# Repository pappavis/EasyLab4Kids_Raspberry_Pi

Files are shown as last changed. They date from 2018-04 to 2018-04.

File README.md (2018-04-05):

### EasyLab Arduino Robotauto
Arduino Robot alles-op-één bordje door **Michiel Erasmus** / EasyLab4Kids. Dit is die tegniese ontwerpe daarvan.<br/>

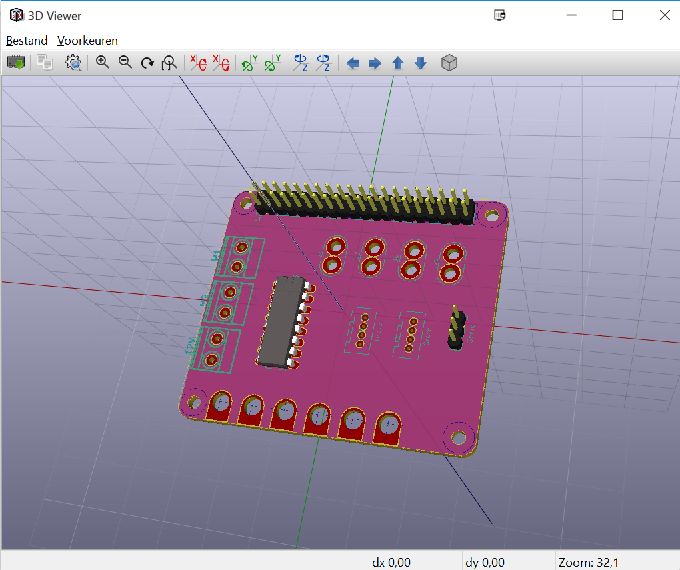
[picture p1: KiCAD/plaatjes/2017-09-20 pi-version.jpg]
<br/>

Credits:
---
**Ontwerp** deur Michiel Erasmus<br/>
**Kontak** thebapodcast@gmail.com<br/>
**Voorbeelde** https://www.facebook.com/EasyBlocks4Kids/<br/>
<br/>

EasyLab basis
---
Wat maak die EasyLab so besonder?<br/>
 - Robotauto op die planeet **MARS!!**
 - Volledig praktyk getest op kinders in Nederland<br/>
 - Beskikbaar met online lesmateriaal in Zuid-Afrikaans en Nederlands<br/>
 
EasyLab tegniese moontlikhede
---
Vir mense met 'n computer brein..<br/>
 - Support vir 2x robotmotors<br/>
 - 1x servo aansluiting<br/>
 - 2x Lynvolg snesore aansluitinge
 - 7x koperplaat aansluiting om maklik 'goedkope' aliexpress-sensore te kan gebruik<br/>
 - Skroefverbindinge vir robotmotors<br/>
 - GPIO en IO-poorte is almal beskikbaar
 - Beskikbaar in twee smake: Arduino en Raspberry Pi<br/>
 <br/>
 Elke EasyLab wordt ambagtelik in Den Haag, Nederland gemaak deur personeel met 'n mentaal of fysieke beperking. Dit help mee aan 'n menswaardig bestaan.<br/>

Self probeer?
---
kyk dan op https://www.facebook.com/EasyBlocks4Kids/ <br/>
<br/>
**EasyLab4Kids met LCD skerm en afstandmeting sensor;**<br/>
<br/>
<br/>
**EasyLab nuusgierige by CoderDojo Den Haag, Nederland [Jun-2017]**<br/>
<br/>
<br/>
Wil jy ook 'n EasyLab? Kontak thebapodcast@gmail.com<br/>
<br/>
<br/>
#easylab4kids #easyblocks4kids #arduinorobot
<br/>

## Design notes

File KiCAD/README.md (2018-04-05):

EasyLab: Raspberry Pi Edition
--
Dit is die printplaat ontwerp vir EasyLab pi editie.

**Credits:**<br/>
Ontwikkeld deur **Michiel Erasmus**.<br/>
Printplaat ontwerp deur **hemalchevli** op fiverr.com<br/>
<br/>
<br/>
**Copyrights**<br/>
GPLV2 license.<br/>
Noem my Michiel Erasmus in jouw credits.<br/>
<br/>
<br/>
<br/>
Printplaat;<br/>
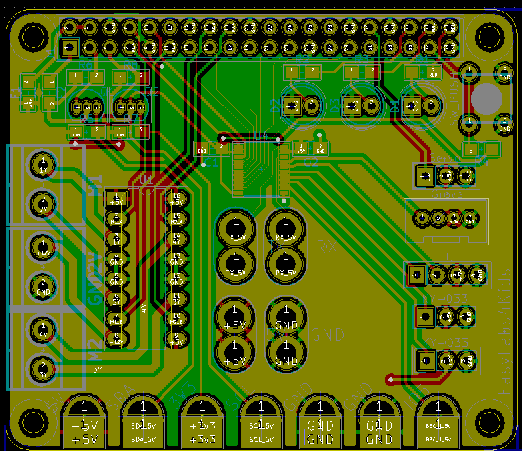
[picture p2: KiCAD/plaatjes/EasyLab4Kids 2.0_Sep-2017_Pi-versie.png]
<br/>
<br/>
#easylab4Kids #easyblocks4kids #erasmus-ict.nl #arduinorobot<br/>

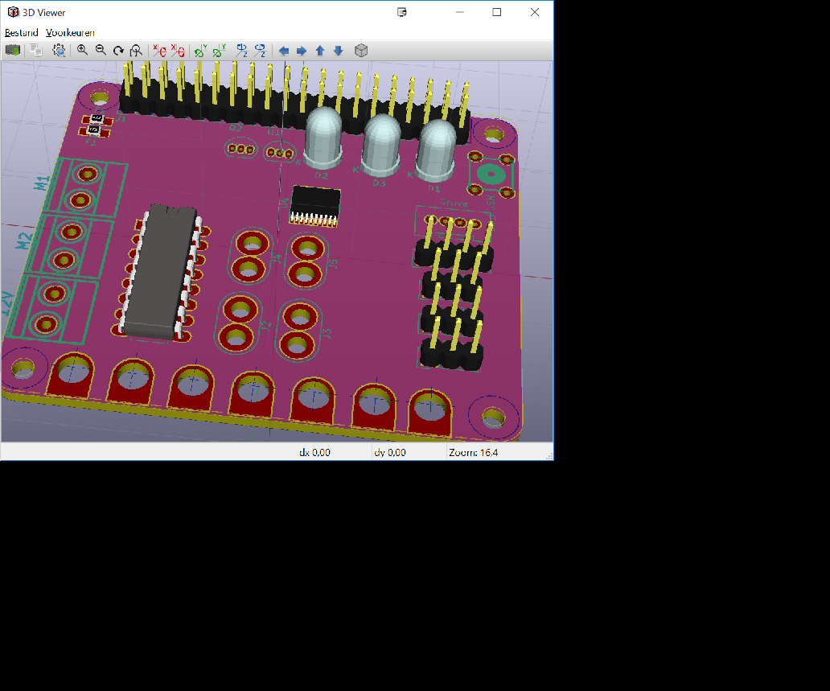
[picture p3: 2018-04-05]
KiCAD/plaatjes/__dev/EasyLab4Kids_Pi_0.0.2.png

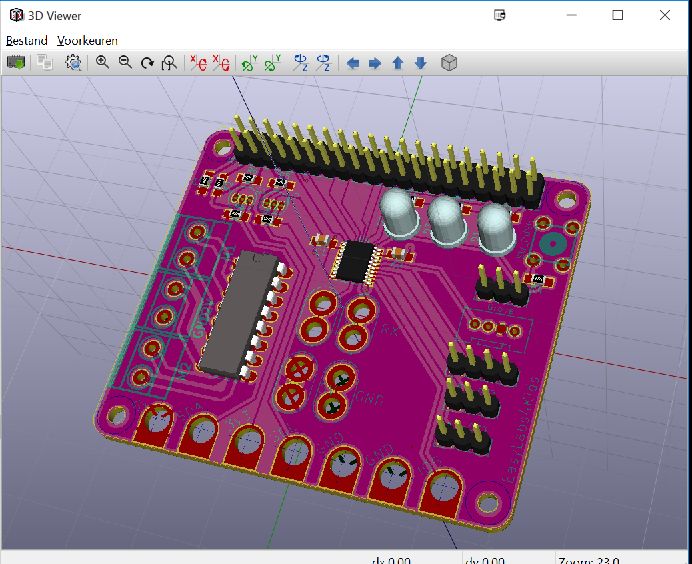
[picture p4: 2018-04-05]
KiCAD/plaatjes/EasyLab4Kids_Pi.jpg

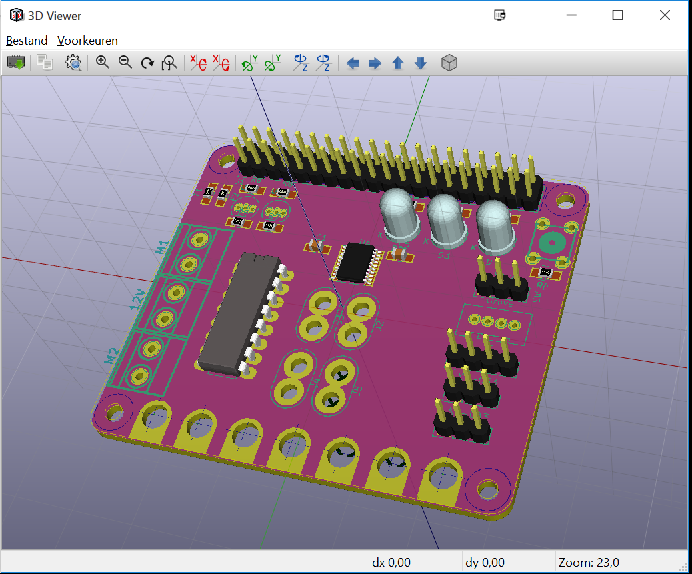
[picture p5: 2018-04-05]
KiCAD/plaatjes/__dev/EasyLab4Kids_Pi_0.0.3_update5.png

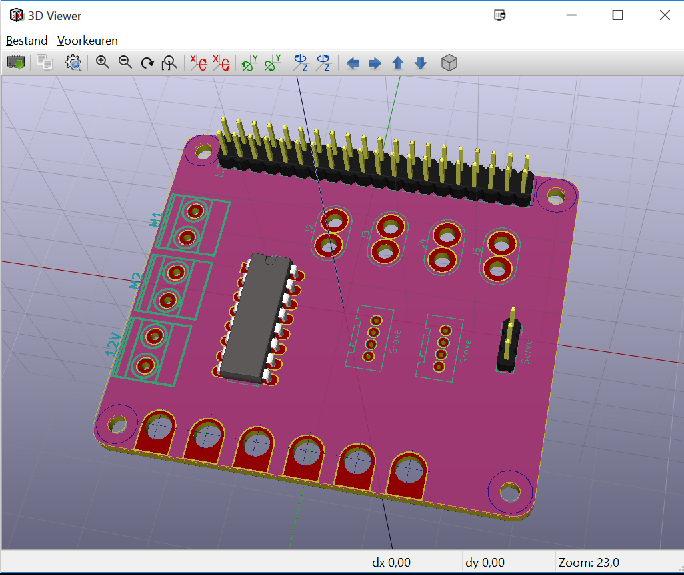
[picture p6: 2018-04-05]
KiCAD/plaatjes/__dev/EasyLab4Kids_Pi_0.0.1_update1.png

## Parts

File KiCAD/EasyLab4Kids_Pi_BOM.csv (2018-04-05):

Title | EasyLabs4Kids
Revision | 0
Date | 2017-09-21
Generated | 11-1-2018 13:44:21
Company
Comment 1 | Drawn by Hemal C [from Fiverr]
Comment 2
Comment 3
Comment 4
Total Parts | 40
Total Unique Parts | 26
Ref | Qty | Value | Footprint | MANF# | manf#
C1 C2 | 2 | 0.1uF | EasyLab4Kids_Pi:C_0805_HandSoldering
D3 D1 D2 | 3 | LED | EasyLab4Kids_Pi:LED-5MM
F1 | 1 | Polyfuse | EasyLab4Kids_Pi:R_0805_HandSoldering | 0ZCK0100FF2E
F2 | 1 | Polyfuse | EasyLab4Kids_Pi:R_0805_HandSoldering |  | 0ZCK0100FF2E
J6 | 1 | 5V | EasyLab4Kids_Pi:BBC_CONNECTOR
J7 J9 | 2 | GND | EasyLab4Kids_Pi:BBC_CONNECTOR
J8 | 1 | 3V3 | EasyLab4Kids_Pi:BBC_CONNECTOR
J10 J11 J18 | 3 | IO | EasyLab4Kids_Pi:BBC_CONNECTOR
J15 | 1 | M1 | EasyLab4Kids_Pi:mkds_1 | 5-2
J16 | 1 | 12V | EasyLab4Kids_Pi:mkds_1 | 5-2
J17 | 1 | M2 | EasyLab4Kids_Pi:mkds_1 | 5-2
J14 | 1 | Servo | EasyLab4Kids_Pi:Pin_Header_Straight_1x03
J2 | 1 | RX | EasyLab4Kids_Pi:Makey_conn
J3 | 1 | TX | EasyLab4Kids_Pi:Makey_conn
J4 | 1 | 5V | EasyLab4Kids_Pi:Makey_conn
J5 | 1 | GND | EasyLab4Kids_Pi:Makey_conn
J1 | 1 | RPi_Header | EasyLab4Kids_Pi:Pin_Header_Straight_2x20
J12 | 1 | Grove | EasyLab4Kids_Pi:grove_1x04
J19 | 1 | IO | EasyLab4Kids_Pi:Pin_Header_Straight_1x04
Q2 Q1 | 2 | 2N7000 | EasyLab4Kids_Pi:TO-92_Inline_Narrow_Oval
R3 R1 R2 | 3 | 330 | EasyLab4Kids_Pi:R_0805_HandSoldering
R4 R7 R8 R5 R6 | 5 | 10K | EasyLab4Kids_Pi:R_0805_HandSoldering
SW1 | 1 | SW_PUSH | EasyLab4Kids_Pi:PCB_PUSH_edit
U1 | 1 | L293D | EasyLab4Kids_Pi:DIP-16_W7.62mm_LongPads
U2 U3 | 2 | KY-033 | EasyLab4Kids_Pi:Pin_Header_Straight_1x03
U4 | 1 | TXB0108 | EasyLab4Kids_Pi:SSOP-20_4.4x6.5mm_Pitch0.65mm
BOM made with KICAD_BOM_WIZARD (https://github.com/HashDefineElectronics/KiCad_BOM_Wizard.git)
Generated 11-1-2018 13:44:21

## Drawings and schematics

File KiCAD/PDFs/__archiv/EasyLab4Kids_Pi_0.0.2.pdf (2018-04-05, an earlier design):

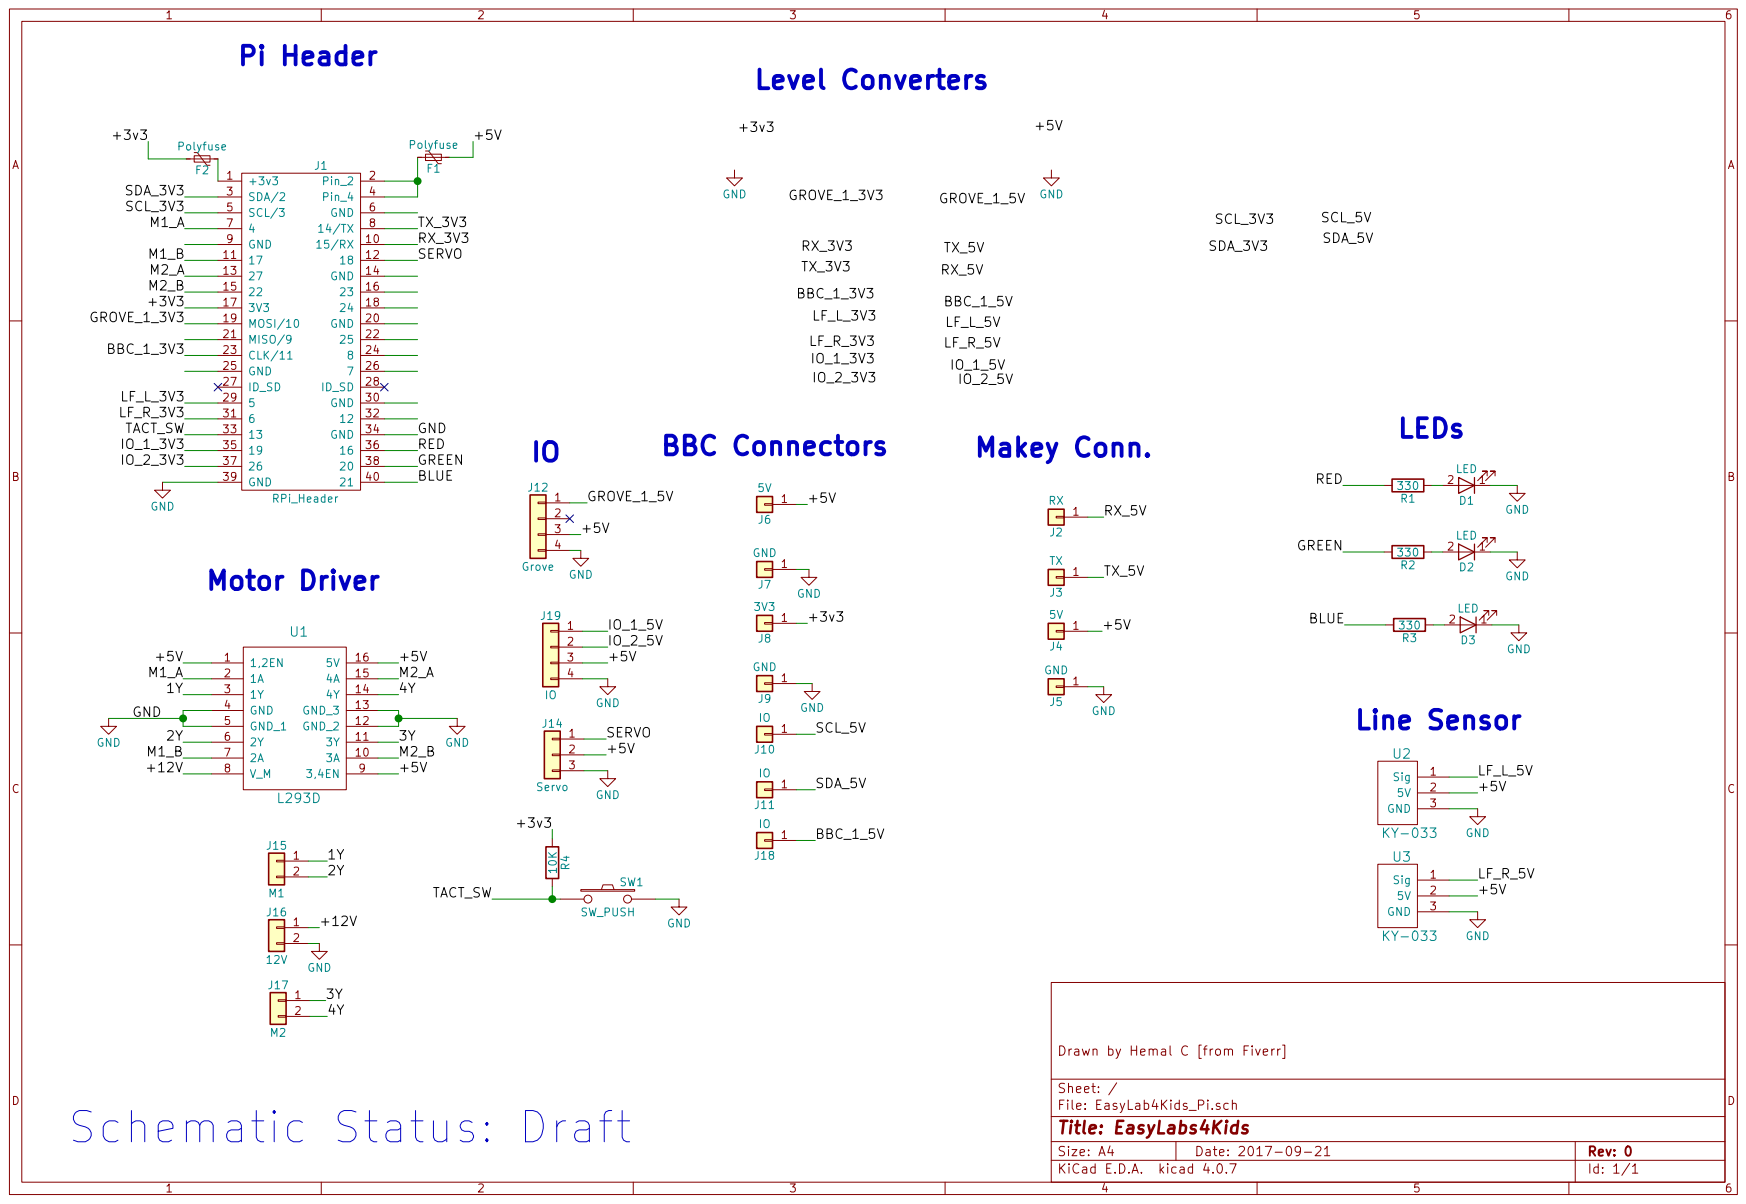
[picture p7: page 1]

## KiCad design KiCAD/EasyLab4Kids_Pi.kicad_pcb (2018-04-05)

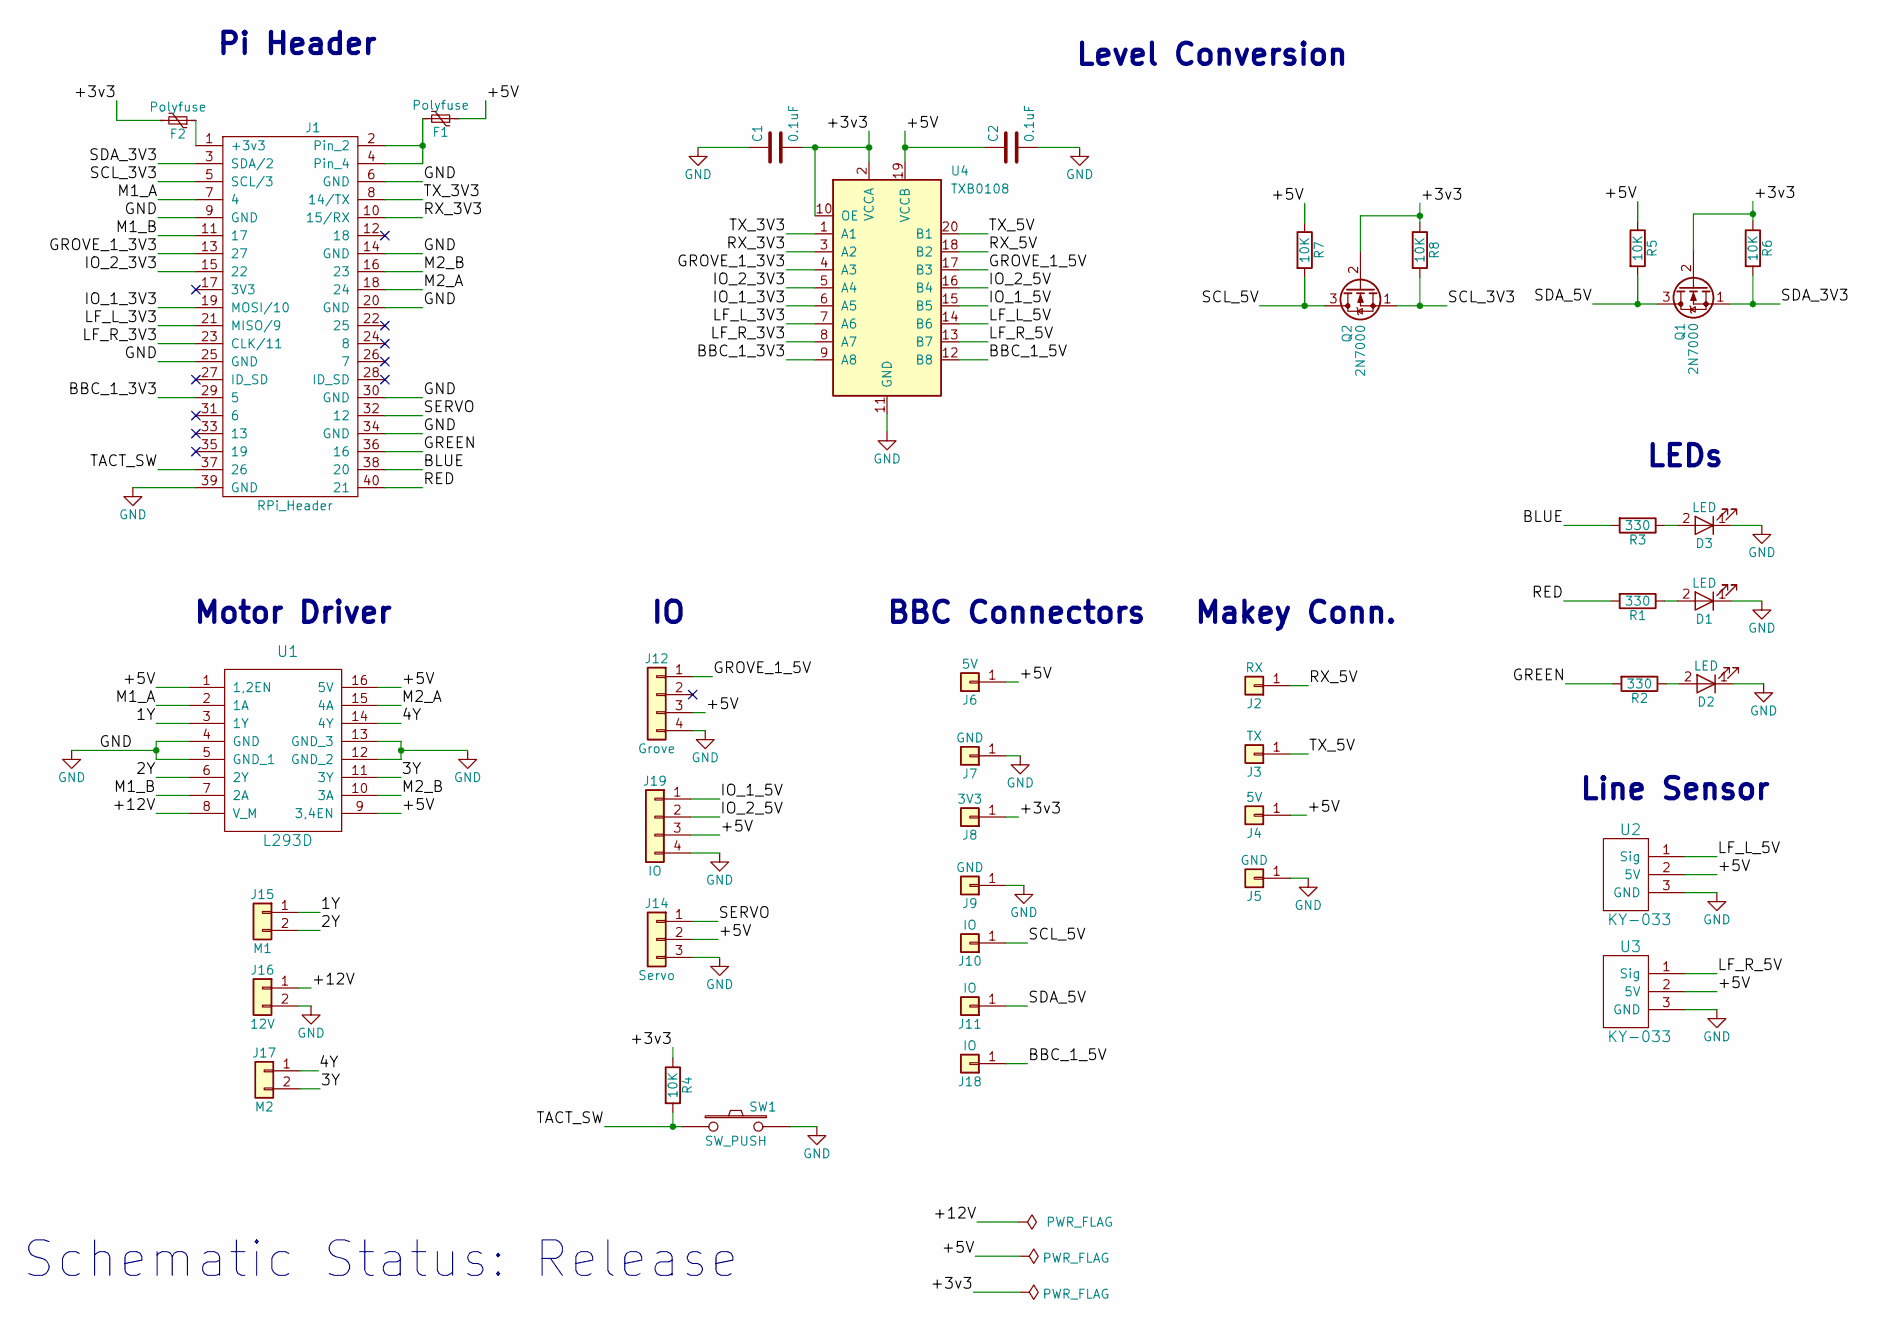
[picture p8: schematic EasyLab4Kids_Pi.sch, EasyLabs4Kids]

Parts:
C1, C2: 0.1uF; C_0805_HandSoldering
D1, D2, D3: LED; LED-5MM
F1, F2: Polyfuse; R_0805_HandSoldering
J1: RPi_Header; Pin_Header_Straight_2x20
J2: RX; Makey_conn
J3: TX; Makey_conn
J4: 5V; Makey_conn
J5: GND; Makey_conn
J6: 5V; BBC_CONNECTOR
J7, J9: GND; BBC_CONNECTOR
J8: 3V3; BBC_CONNECTOR
J10, J11, J18: IO; BBC_CONNECTOR
J12: Grove; grove_1x04
J14: Servo; Pin_Header_Straight_1x03
J15: M1; mkds_1,5-2
J16: 12V; mkds_1,5-2
J17: M2; mkds_1,5-2
J19: IO; Pin_Header_Straight_1x04
Q1, Q2: 2N7000; TO-92_Inline_Narrow_Oval
R1, R2, R3: 330; R_0805_HandSoldering
R4, R5, R6, R7, R8: 10K; R_0805_HandSoldering
SW1: SW_PUSH; PCB_PUSH_edit
U1: L293D; DIP-16_W7.62mm_LongPads
U2, U3: KY-033; Pin_Header_Straight_1x03
U4: TXB0108; SSOP-20_4.4x6.5mm_Pitch0.65mm

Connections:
/1Y: J15.1, U1.3 (1Y)
/2Y: J15.2, U1.6 (2Y)
/3Y: J17.2, U1.11 (3Y)
/4Y: J17.1, U1.14 (4Y)
/+3v3: C1.2, F2.2, J8.1, Q1.2 (G), Q2.2 (G), R4.1, R6.1, R8.1, U4.2 (VCCA), U4.10 (OE)
/+5V: C2.1, F1.1, J4.1, J6.1, J12.3, J14.2, J19.3, R5.1, R7.1, U1.1 (1,2EN), U1.9 (3,4EN), U1.16 (5V), U2.2 (5V), U3.2 (5V), U4.19 (VCCB)
/+12V: J16.1, U1.8 (V_M)
/BBC_1_3V3: J1.29 (5), U4.9 (A8)
/BBC_1_5V: J18.1, U4.12 (B8)
/BLUE: J1.38 (20), R3.2
/GREEN: J1.36 (16), R2.2
/GROVE_1_3V3: J1.13 (27), U4.4 (A3)
/GROVE_1_5V: J12.1, U4.17 (B3)
/IO_1_3V3: J1.19 (MOSI/10), U4.6 (A5)
/IO_1_5V: J19.1, U4.15 (B5)
/IO_2_3V3: J1.15 (22), U4.5 (A4)
/IO_2_5V: J19.2, U4.16 (B4)
/LF_L_3V3: J1.21 (MISO/9), U4.7 (A6)
/LF_L_5V: U2.1 (Sig), U4.14 (B6)
/LF_R_3V3: J1.23 (CLK/11), U4.8 (A7)
/LF_R_5V: U3.1 (Sig), U4.13 (B7)
/M1_A: J1.7 (4), U1.2 (1A)
/M1_B: J1.11 (17), U1.7 (2A)
/M2_A: J1.18 (24), U1.15 (4A)
/M2_B: J1.16 (23), U1.10 (3A)
/RED: J1.40 (21), R1.2
/RX_3V3: J1.10 (15/RX), U4.3 (A2)
/RX_5V: J2.1, U4.18 (B2)
/SCL_3V3: J1.5 (SCL/3), Q2.1 (S), R8.2
/SCL_5V: J10.1, Q2.3 (D), R7.2
/SDA_3V3: J1.3 (SDA/2), Q1.1 (S), R6.2
/SDA_5V: J11.1, Q1.3 (D), R5.2
/SERVO: J1.32 (12), J14.1
/TACT_SW: J1.37 (26), R4.2, SW1.1
/TX_3V3: J1.8 (14/TX), U4.1 (A1)
/TX_5V: J3.1, U4.20 (B1)
GND: C1.1, C2.2, D1.1 (K), D2.1 (K), D3.1 (K), J1.6 (GND), J1.9 (GND), J1.14 (GND), J1.20 (GND), J1.25 (GND), J1.30 (GND), J1.34 (GND), J1.39 (GND), J5.1, J7.1, J9.1, J12.4, J14.3, J16.2, J19.4, SW1.2, U1.4 (GND), U1.5 (GND_1), U1.12 (GND_2), U1.13 (GND_3), U2.3 (GND), U3.3 (GND), U4.11 (GND)
unnamed: D1.2 (A), R1.1
unnamed: D2.2 (A), R2.1
unnamed: D3.2 (A), R3.1
unnamed: F1.2, J1.2, J1.4
unnamed: F2.1, J1.1 (+3v3)

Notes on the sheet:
Schematic Status: Release
BBC Connectors
Motor Driver
Pi Header
Makey Conn.
Level Conversion
Line Sensor
LEDs

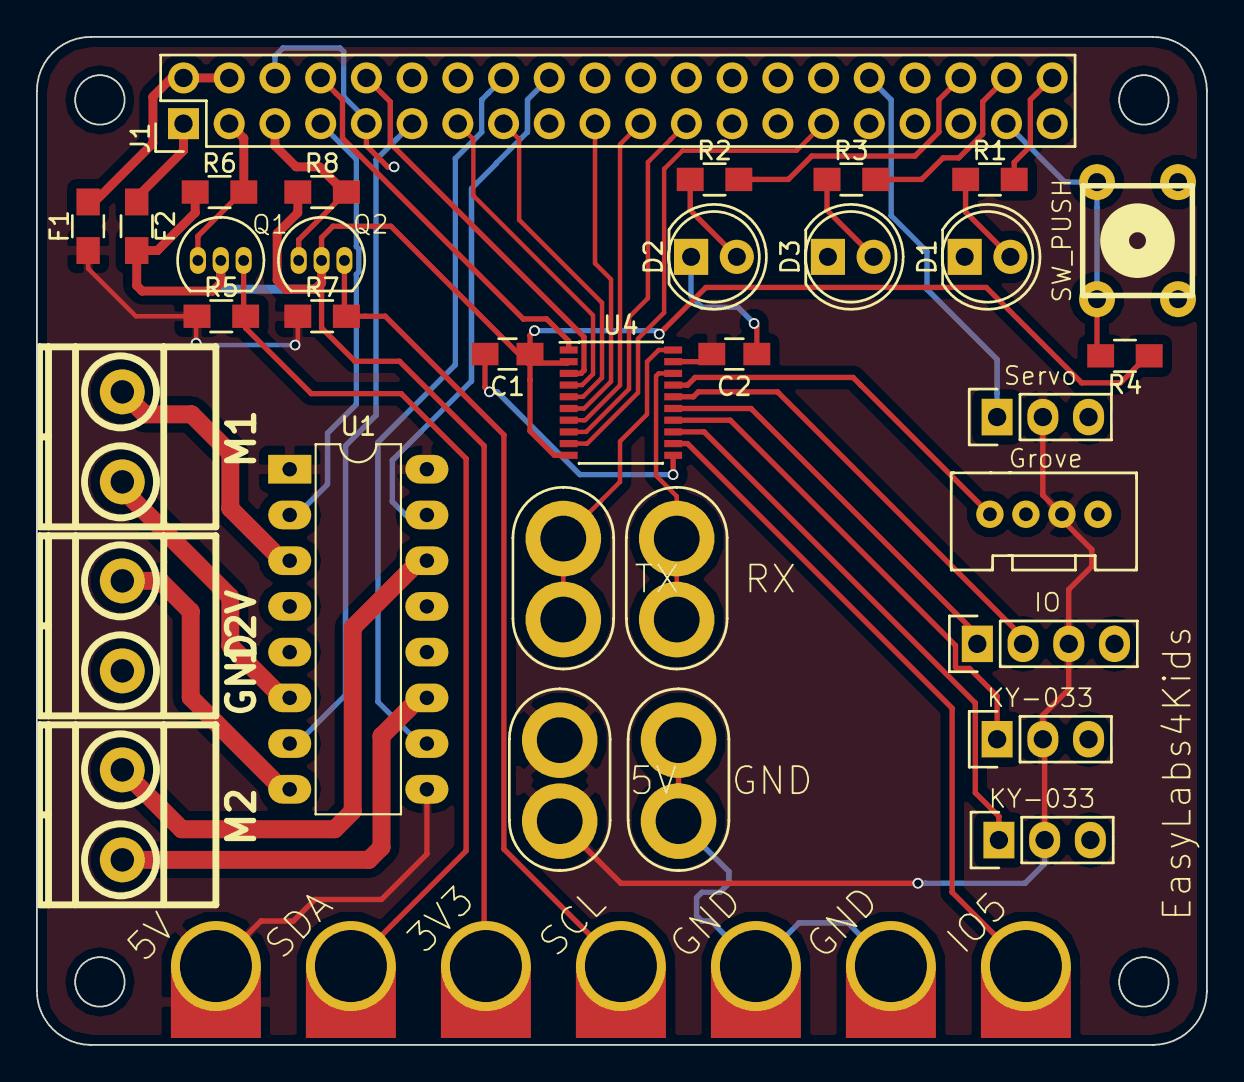
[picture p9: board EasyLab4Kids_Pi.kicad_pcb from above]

Board: 2 copper layers, 65.0 x 56.0 mm, 40 parts (0 on the bottom side), 42 nets.
